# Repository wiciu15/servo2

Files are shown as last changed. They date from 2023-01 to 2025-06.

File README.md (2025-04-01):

# Servo 2
## 3-phase AC servomotor driver

This is a project of a servo inverter to drive 3-phase AC motor with/out encoder feedback

It's in alpha development so there are many bugs and things included in software but not really working/tested.

DEMO video: https://www.youtube.com/watch?v=Hu02lt5aCbM

CNC DEMO: https://www.youtube.com/watch?v=LXm4no8DIPE

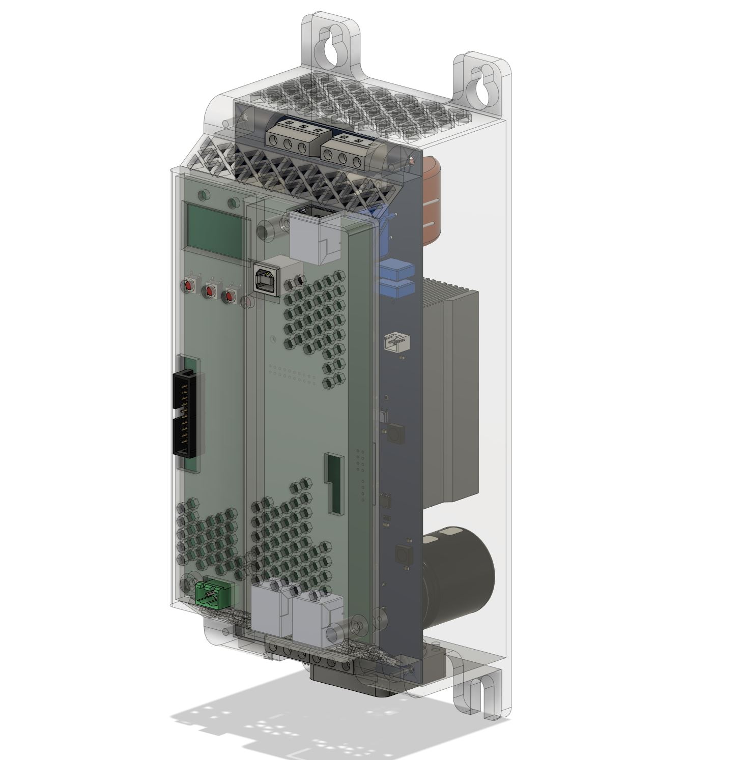
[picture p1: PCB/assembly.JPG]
CPU board


This is a free software under the GNU license, you can redistribute it and/or modify it under the terms
of the GNU General Public License version 3 as published by the Free Software Foundation.
This project is shared with public for educational purposes, without WARRANTY and Author is not liable for any damages caused directly
or indirectly by this software/hardware. The board is mains-powered. High voltage can kill you. Have caution when using high voltage devices

## Features

- Manual voltage and frequency control
- U/f scalar motor control
- Open loop current control for test purposes
- Field-oriented vector control (FOC) for PMSM/BLDC motors with encoder feedback
- Encoders support:
  -  ABZ encoder with differential driver output, needs one manual rotation to index with a rotor properly
  -  Mitsubishi J2/J2s/J4/JE series, baud rate 2 500 000 bits/s, implementation is working but need some polish
  -  Tamagawa T-Format encoders - tested with ABB BSM-series motor, baud rate 2 500 000 bits/s, most robust implementation and testing at this moment
  -  Panasonic minas series encoder - support in early development, not much tested and buggy
  -  DELTA NH4 series T+ T- encoder - very early development
- Braking chopper control
- under/overvoltage, overcurrent, short-circuit and other errors detection and handling
- Communication with PC using MODBUS over USB-CDC
- simple CANopen node for fieldbus control
- Parameter set, with non-volatile storage in external EEPROM
- control and monitoring of drive using OLED screen and buttons
- ramp generators and limiters for current,speed and position control loops

## To-do in the future

- I2t thermal monitoring of motor
- sensorless rotor angle aquisition
- analog and digital I/O
- step/dir input
- current and speed loop gains auto-tuning
- motor parameters automatic measurement

## Used third-party software
- I2C EEPROM driver by ControllersTech
- OLED driver https://github.com/afiskon/stm32-ssd1306
- stModbus https://github.com/wiciu15/stModbus/
- CANopenNode https://github.com/CANopenNode/CANopenNode
- embedded printf implementation https://github.com/mpaland/printf
- FreeRTOS

## Hardware modification
MOdifications of rev.A of CPU board
- data/command line to OLED screen(PA15)
- bridge between tim1break input (PE15) and overcurrent interrupt(PA1)(break interrupt was not working i dont know why just bridged it to EXTI on other pin).
- OLED CLK is moved to PA5, PB3 is used as DEBUG_SWO.
- added filter to GND on FAULT line from power board to enchance noise rejection from EMI(i was getting random short-circuit errors).

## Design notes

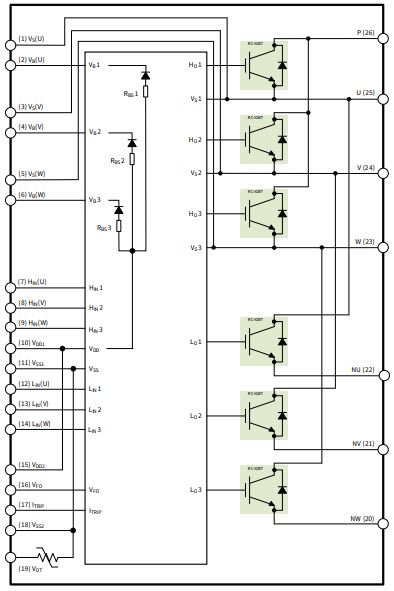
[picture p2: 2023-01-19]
PCB/servo_pwr/Infineon IPM.JPG

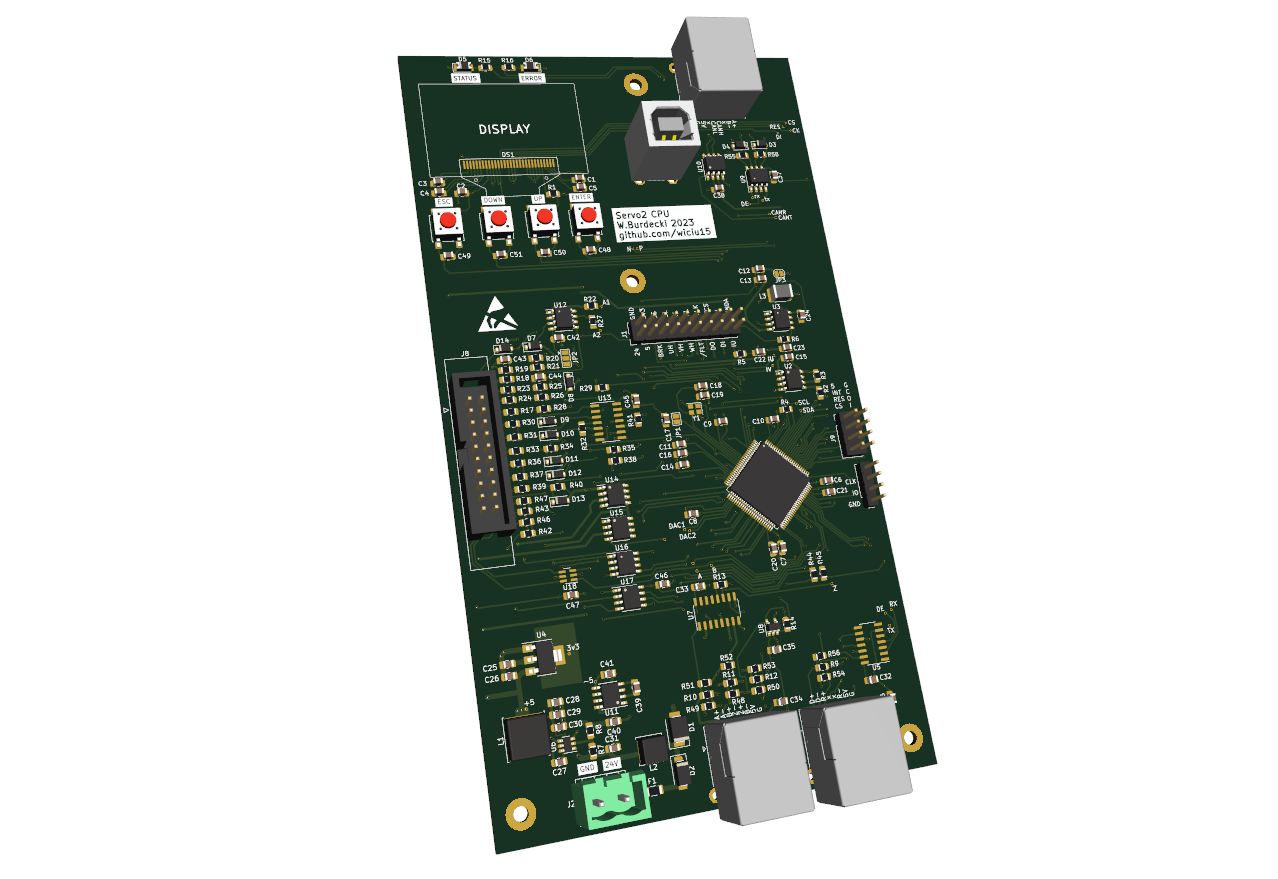
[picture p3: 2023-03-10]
PCB/servo_cpu/servo_cpu.png

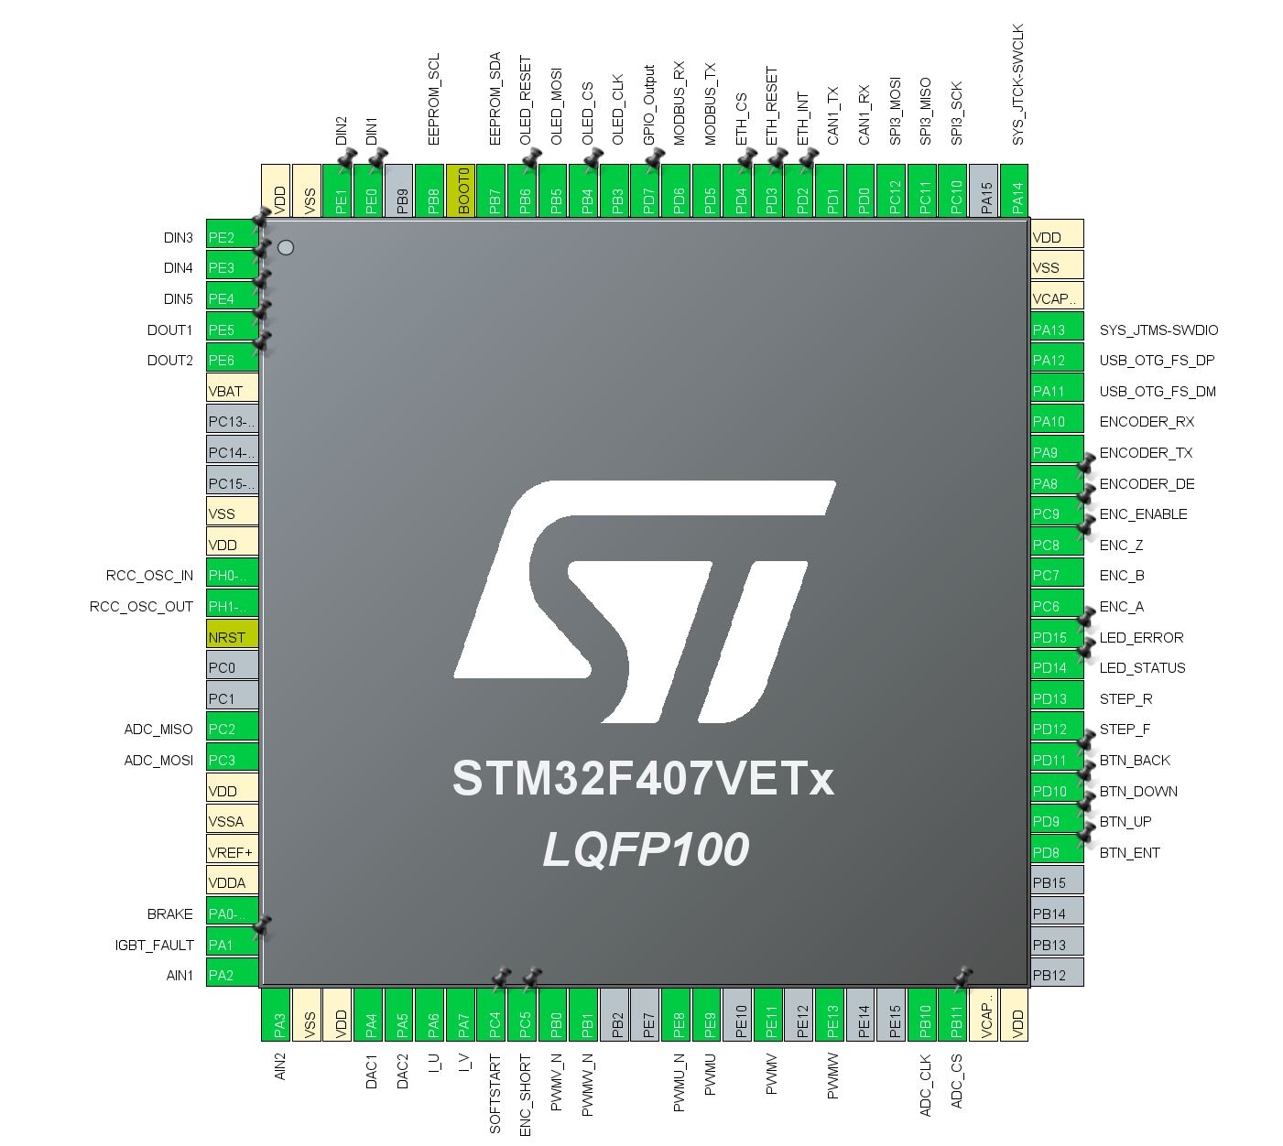
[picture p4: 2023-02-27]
PCB/servo_cpu/piny cpu.JPG

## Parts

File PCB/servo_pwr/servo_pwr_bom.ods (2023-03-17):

Designator | Name | Qt
C1, C3, C4, C5, C6, C7, C8, C11, C12, C13, C14, C15, C16, C17, C18, C19, C20, C21, C22, C23, C25, C30, C34, C36, C37 | 2.2 ﾵF | 25
C2, C9, C26, C27, C35 | 22 ﾵF | 5
C10 | 100 ﾵF | 1
C24 | 10000 pF | 1
C28, C32 | 4700 pF | 2
C29, C33 | 0.1 ﾵF | 2
C31 | 1000 pF | 1
C38 | 470n X2 275V | 1
C39, C40 | 470ﾵF | 2
C41, C42, C44, C45 | 4n7 | 4
C43 | 3.3u/600V | 1
D1 | 10A6 | 1
D2 | 1N4148W-7-F | 1
DB1 | Component_1 | 1
F1 | Fuse | 1
IC1 | LD1117S50TR | 1
IC2 | 2N7002E-7-F | 1
IPM1 | IM323L6G2 | 1
J1, J2, J3, J4 | DG128-7.5-03P-14 | 4
J5 | goldpin | 1
J6 | FAN | 1
J10 | jumper | 1
L1, L2 | 1 mH | 2
L3 | SC-18-25J | 1
MH3, MH4 | Mountinghole_M2,5 | 2
MH5, MH6, MH7, MH8 | Mountinghole_M2,5_nonplated | 4
Q1 | STGW30NC60KD | 1
R1, R2, R3, R4, R5, R6, R13, R20, R21, R22, R29 | 470 Ohms | 11
R7, R10 | 1 kOhms | 2
R8 | 22 kOhms | 1
R9, R25 | 47 Ohms | 2
R11, R12, R14 | 150 mOhms | 3
R15, R16, R17, R18 | 100 kOhms | 4
R19 | 4.7 kOhms | 1
R23, R24 | PRM05WJP333 | 2
R26 | 10 kOhms | 1
R27 | 1M | 1
R28 | PRMAAWJW470B00 | 1
RL1 | G2R-1A-E | 1
RV1 | SIOV-S20K275 | 1
TP1 | 5V | 1
TP2 | FO | 1
TP3 | HU | 1
TP4 | HV | 1
TP5 | HW | 1
TP8 | 15VH | 1
TP9 | OC | 1
TP10 | Gnd | 1
TP11 | 5VH | 1
TP12 | DO | 1
TP13 | G | 1
TP14 | IU | 1
TP15 | 3V3 | 1
TP16 | IV | 1
TP17 | TMP | 1
TP18 | CS | 1
TP19 | DI | 1
TP20 | CK | 1
U1, U3, U4, U5, U6, U7, U8, U9, U11, U13, U15 | TLP2345 | 11
U2 | TBA 2-0513 | 1
U10, U12 | LEM GO10SME/SP3 | 2
U14 | MCP3002-I/SN | 1
U16 | TLP701 | 1

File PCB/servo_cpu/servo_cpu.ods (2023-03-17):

C1, C2, C3, C4, C5, C6, C7, C8, C9, C10, C11, C12,C13, C14, C15, C16, C20, C21, C24, C25, C26, C32, C33, C34, C35, C36, C37, C38, C40, | 29 | 2u2
C17, C27, C42, C43, C44, C45, C46, C47, C48, C49, C50, C51, | 12 | 100n
C18, C19, | 2 | 12p
C22, C23, | 2 | 1u
C28, C29, C30, C31, C39, C41, | 6 | 22u
D1, | 1 | SM6T27A
D2, | 1 | US1B
D3, D4, | 2 | BZT52B6v2
D5, | 1 | GREEN_LED
D6, | 1 | RED_LED
D7, D8, D9, D10, D11, D12, D13, | 7 | BZT52B5v1
D14, | 1 | 1N4148
DS1, | 1 | OLED-128O064D
F1, | 1 | 615mA PTC
J1, | 1 | PWR board
J2, | 1 | Control power
J3, | 1 | ABZ
J4, | 1 | Serial Encoder
J5, | 1 | CONN
J6, | 1 | DEBUG
J7, | 1 | USB_B
J8, | 1 | I/O
J9, | 1 | EXT
JP1, | 1 | RESET
JP2, | 1 | OPA-V
JP3, | 1 | GND
L1, | 1 | 4u7
L2, | 1 | 10u
L3, | 1 | 470u
R1, | 1 | 820k
R2, R3, | 2 | 4,7k
R4, R15, R16, R44, R45, R55, | 6 | 1k
R5, R6, | 2 | 22R
R7, | 1 | 220k
R8, | 1 | 18k
R9, R22, R27, | 3 | 150R
R10, R11, R12, | 3 | 220R
R13, R14, R17, R18, R19, R23, R24, R29, R30, R32, R33, R35, R36, R38, R39, R41, | 16 | 10k
R20, R21, R25, R26, | 4 | 3k3
R28, R31, R34, R37, R40, R42, R43, | 7 | 2k2
R46, R47, R48, R49, R50, R51, R52, R53, R54, R56, R58, | 11 | 470R
SW1, | 1 | ENTER
SW2, | 1 | ESC
SW3, | 1 | UP
SW4, | 1 | DOWN
U1, | 1 | STM32F407VETx
U2, | 1 | M24C02-WMN
U3, U12, U16, | 3 | TS912
U4, | 1 | AP1117-33
U5, | 1 | ISL83491
U6, | 1 | AP63205WU
U7, | 1 | AM26LS32A
U8, | 1 | AP2151A
U9, | 1 | MAX485E
U10, | 1 | SN65HVD232
U11, | 1 | LMC7660
U13, | 1 | 74HC14
U14, U15, | 2 | ISP742RI
U17, | 1 | VO0661T
U18, | 1 | 74LVC2G04
Y1, | 1 | 16M xt224

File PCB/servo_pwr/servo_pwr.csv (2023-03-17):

Line # | Designator | Name | Quantity | Description | Manufacturer 1 | Manufacturer Part Number 1 | Manufacturer Lifecycle 1 | Supplier 1 | Supplier Part Number 1 | Supplier Unit Price 1 | Supplier Subtotal 1
 | C1, C3, C4, C5, C6, C7, C8, C11, C12, C13, C14, C15, C16, C17, C18, C19, C20, C21, C22, C23, C25, C30, C34, C36, C37 | 2.2 µF | 25 | CAP CER 2.2UF 35V X7R 0805 | TDK | C2012X7R1V225K125AB | Volume Production | Digi-Key | 445-7551-1-ND | 0.373 | 9.33
 | C2, C9, C26, C27, C35 | 22 µF | 5 | CAP CER 22UF 16V X5R 0805 | Samsung | CL21A226KOQNNNG | Volume Production | Digi-Key | 1276-7092-1-ND | 0.33 | 1.65
 | C10 | 100 µF | 1 | CAP ALUM 100UF 20% 25V RADIAL | Panasonic | EEUTA1E101 | Volume Production | DigiKey | P19501-ND
 | C24 | 10000 pF | 1 | CAP CER 0805 10NF 50V X7R 10% | KEMET | C0805C103K5RECAUTO | Unknown | Digi-Key | 399-17885-1-ND | 0.25 | 0.25
 | C28, C32 | 4700 pF | 2 | CAP CER 0805 4.7NF 50V X7R 10% | KEMET | C0805C472K5RECAUTO | Unknown | DigiKey | 399-17884-1-ND
 | C29, C33 | 0.1 µF | 2 | CAP CER 0.1UF 50V X7R 0805 | Yageo | CC0805MRX7R9BB104 | Volume Production | Digi-Key | 311-4351-1-ND | 0.13 | 0.26
 | C31 | 1000 pF | 1 | CAP CER 0805 1NF 50V ULTRA STABL | KEMET | C0805X102J5HACAUTO | Unknown | Digi-Key | 399-16876-1-ND | 0.22 | 0.22
 | C38 | 470n X2 275V | 1 | KEMET R46KI347050M1K
 | C39, C40 | 470µF | 2 | CAP ALUM 470UF 20% 450V SNAP | Rubycon | 450HXG470MEFCSN35X45 | Volume Production | Digi-Key | 1189-1975-ND | 11.39 | 22.78
 | C41, C42, C44, C45 | 4n7 | 4 | B32021A3472
 | C43 | 3.3u/600V | 1
 | D1 | 10A6 | 1
 | D2 | 1N4148W-7-F | 1 | DIODE GEN PURP 100V 300MA SOD123 | Diodes | 1N4148W-7-F | Unknown | Digi-Key | 1N4148W-FDICT-ND | 0.17 | 0.17
 | DB1 | Component_1 | 1
 | F1 | Fuse | 1 | Fuse holder 04450001N
 | IC1 | LD1117S50TR | 1 | IC REG LINEAR 5V 800MA SOT223 | STMicroelectronics | LD1117S50TR | Unknown | Digi-Key | 497-6447-1-ND | 0.66 | 0.66
 | IC2 | 2N7002E-7-F | 1 | MOSFET N-CH 60V 0.25A SOT23-3 | Diodes | 2N7002E-7-F | Volume Production | DigiKey | 2N7002E-FDICT-ND
 | IPM1 | IM323L6G2 | 1
 | J1, J2, J3, J4 | DG128-7.5-03P-14 | 4
 | J5 | goldpin | 1
 | J6 | FAN | 1
 | J10 | jumper | 1
 | L1, L2 | 1 mH | 2 | FIXED IND 1MH 150MA 4.5 OHM SMD | Bourns | SRR6028-102Y | Volume Production | DigiKey | SRR6028-102YCT-ND
 | L3 | SC-18-25J | 1 | https://www.tme.eu/pl/details/sc-18-25j/dlawiki-pierscieniowe/kemet/
 | MH3, MH4 | Mountinghole_M2,5 | 2
 | MH5, MH6, MH7, MH8 | Mountinghole_M2,5_nonplated | 4
 | Q1 | STGW30NC60KD | 1
 | R1, R2, R3, R4, R5, R6, R13, R20, R21, R22, R29 | 470 Ohms | 11 | RES SMD 470 OHM 0.1% 1/4W 0805 | Panasonic | ERJ-PB6B4700V | New Product | Digi-Key | P20556CT-ND | 0.338 | 3.72
 | R7, R10 | 1 kOhms | 2 | RES 1K OHM 0.1% 1/10W 0805 | Stackpole Electronics | RNCS0805BKE1K00 | Volume Production | Digi-Key | RNCS0805BKE1K00CT-ND | 0.52 | 1.04
 | R8 | 22 kOhms | 1 | RES 22K OHM 5% 1/8W 0805 | TE Connectivity | CRGCQ0805J22K | Unknown | Digi-Key | A130142CT-ND | 0.1 | 0.1
 | R9, R25 | 47 Ohms | 2 | RES 47 OHM 1% 1/3W 0805 | TE Connectivity | CRGP0805F47R | Unknown | Digi-Key | A130461CT-ND | 0.22 | 0.44
 | R11, R12, R14 | 150 mOhms | 3 | RES 150M OHM 1% 2W 2512 | KOA Speer | TLRH3AWTTER150F | Volume Production | Digi-Key | 2019-TLRH3AWTTER150FCT-ND | 1.48 | 4.44
 | R15, R16, R17, R18 | 100 kOhms | 4 | RES SMD 100K OHM 0.1% 1/4W 1206 | Yageo | RT1206BRB07100KL | Volume Production | Digi-Key | YAG5016CT-ND | 0.75 | 3
 | R19 | 4.7 kOhms | 1 | RES SMD 4.7K OHM 1% 1/4W 1206 | TE Connectivity | CRG1206F4K7 | Volume Production | Digi-Key | A106078CT-ND | 0.1 | 0.1
 | R23, R24 | PRM05WJP333 | 2
 | R26 | 10 kOhms | 1 | RES 10K OHM 0.1% 1/10W 0805 | Stackpole Electronics | RNCS0805BKE10K0 | Volume Production | Digi-Key | RNCS0805BKE10K0CT-ND | 0.52 | 0.52
 | R27 | 1M | 1 | Resistor
 | R28 | PRMAAWJW470B00 | 1 | https://www.tme.eu/pl/details/ax10wv-47r/rezystory-mocy/royal-ohm/prmaawjw470b00/
 | RL1 | G2R-1A-E | 1 | https://www.tme.eu/pl/details/g2r-1a-e-24dc/przekazniki-elektromagn-miniaturowe/omron-ocb/g2r-1a-e-24vdc/
 | RV1 | SIOV-S20K275 | 1 | B72220S0271K101
 | TP1 | 5V | 1
 | TP2 | FO | 1
 | TP3 | HU | 1
 | TP4 | HV | 1
 | TP5 | HW | 1
 | TP8 | 15VH | 1
 | TP9 | OC | 1
 | TP10 | Gnd | 1
 | TP11 | 5VH | 1
 | TP12 | DO | 1
 | TP13 | G | 1
 | TP14 | IU | 1
 | TP15 | 3V3 | 1
 | TP16 | IV | 1
 | TP17 | TMP | 1
 | TP18 | CS | 1
 | TP19 | DI | 1
 | TP20 | CK | 1
 | U1, U3, U4, U5, U6, U7, U8, U9, U11, U13, U15 | TLP2345 | 11
 | U2 | TBA 2-0513 | 1 | No Description Available
 | U10, U12 | LEM GO10SME/SP3 | 2
 | U14 | MCP3002-I/SN | 1 | No Description Available
 | U16 | TLP701 | 1

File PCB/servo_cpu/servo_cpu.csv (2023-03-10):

Source: | C:\Users\Wiktor\Documents\servo2pcb\PCB\servo_cpu\servo_cpu.kicad_sch
Date: | 10.03.2023 15:43:41
Tool: | Eeschema (7.0.0)
Generator: | C:\Program Files\KiCad\6.0\bin\scripting\plugins/bom_csv_grouped_by_value_with_fp.py
Component Count: | 162
Ref | Qnty | Value | Cmp name | Footprint | Description | Vendor
C1, C2, C3, C4, C5, C6, C7, C8, C9, C10, C11, C12, C13, C14, C15, C16, C20, C21, C24, C25, C26, C32, C33, C34, C35, C36, C37, C38, C40, | 29 | 2u2 | C_Small | Capacitor_SMD:C_0805_2012Metric_Pad1.18x1.45mm_HandSolder | Unpolarized capacitor, small symbol
C17, C27, C42, C43, C44, C45, C46, C47, C48, C49, C50, C51, | 12 | 100n | C_Small | Capacitor_SMD:C_0805_2012Metric_Pad1.18x1.45mm_HandSolder | Unpolarized capacitor, small symbol
C18, C19, | 2 | 12p | C_Small | Capacitor_SMD:C_0805_2012Metric_Pad1.18x1.45mm_HandSolder | Unpolarized capacitor, small symbol
C22, C23, | 2 | 1u | C_Small | Capacitor_SMD:C_0805_2012Metric_Pad1.18x1.45mm_HandSolder | Unpolarized capacitor, small symbol
C28, C29, C30, C31, C39, C41, | 6 | 22u | C_Small | Capacitor_SMD:C_0805_2012Metric_Pad1.18x1.45mm_HandSolder | Unpolarized capacitor, small symbol
D1, | 1 | SM6T27A | SM6T27A | Diode_SMD:D_SMB | 600W unidirectional Transil Transient Voltage Suppressor, 27Vrwm, DO-214AA
D2, | 1 | US1B | US1B | Diode_SMD:D_SMA | 100V, 1A, General Purpose Rectifier Diode, SMA(DO-214AC)
D3, D4, | 2 | BZT52B6v2 | BZT52Bxx | Diode_SMD:D_SOD-123F | 500mW Zener Diode, SOD-123F
D5, | 1 | GREEN_LED | LED | Diode_SMD:D_1206_3216Metric_Pad1.42x1.75mm_HandSolder | Light emitting diode
D6, | 1 | RED_LED | LED | Diode_SMD:D_1206_3216Metric_Pad1.42x1.75mm_HandSolder | Light emitting diode
D7, D8, D9, D10, D11, D12, D13, | 7 | BZT52B5v1 | BZT52Bxx | Diode_SMD:D_SOD-123F | 500mW Zener Diode, SOD-123F
D14, | 1 | 1N4148 | D_Small | Diode_SMD:D_SOD-123F | Diode, small symbol
DS1, | 1 | OLED-128O064D | OLED-128O064D | Display:OLED-128O064D | OLED display 128x64
F1, | 1 | 615mA PTC | Fuse | Fuse:Fuse_1206_3216Metric | Fuse
J1, | 1 | PWR board | Conn_02x10_Counter_Clockwise | Connector_PinHeader_2.54mm:PinHeader_2x10_P2.54mm_Vertical | Generic connector, double row, 02x10, counter clockwise pin numbering scheme (similar to DIP package numbering), script generated (kicad-library-utils/schlib/autogen/connector/)
J2, | 1 | Control power | Screw_Terminal_01x02 | TerminalBlock_RND:TerminalBlock_RND_205-00232_1x02_P5.08mm_Horizontal | Generic screw terminal, single row, 01x02, script generated (kicad-library-utils/schlib/autogen/connector/)
J3, | 1 | ABZ | 8P8C_Shielded | Connector_RJ:RJ45_Ninigi_GE | RJ connector, 8P8C (8 positions 8 connected), RJ31/RJ32/RJ33/RJ34/RJ35/RJ41/RJ45/RJ49/RJ61, Shielded
J4, | 1 | Serial Encoder | 8P8C_Shielded | Connector_RJ:RJ45_Ninigi_GE | RJ connector, 8P8C (8 positions 8 connected), RJ31/RJ32/RJ33/RJ34/RJ35/RJ41/RJ45/RJ49/RJ61, Shielded
J5, | 1 | CONN | 8P8C_Shielded | Connector_RJ:RJ45_Ninigi_GE | RJ connector, 8P8C (8 positions 8 connected), RJ31/RJ32/RJ33/RJ34/RJ35/RJ41/RJ45/RJ49/RJ61, Shielded
J6, | 1 | DEBUG | Conn_01x04 | Connector_PinHeader_2.54mm:PinHeader_1x04_P2.54mm_Vertical | Generic connector, single row, 01x04, script generated (kicad-library-utils/schlib/autogen/connector/)
J7, | 1 | USB_B | USB_B | USB_B_JST_Vertical:USB | USB Type B connector
J8, | 1 | I/O | Conn_02x10_Odd_Even | Connector_IDC:IDC-Header_2x10_P2.54mm_Latch_Vertical | Generic connector, double row, 02x10, odd/even pin numbering scheme (row 1 odd numbers, row 2 even numbers), script generated (kicad-library-utils/schlib/autogen/connector/)
J9, | 1 | EXT | Conn_02x04_Odd_Even | Connector_PinHeader_2.54mm:PinHeader_2x04_P2.54mm_Horizontal | Generic connector, double row, 02x04, odd/even pin numbering scheme (row 1 odd numbers, row 2 even numbers), script generated (kicad-library-utils/schlib/autogen/connector/)
JP1, | 1 | RESET | SolderJumper_2_Open | Jumper:SolderJumper-2_P1.3mm_Open_Pad1.0x1.5mm | Solder Jumper, 2-pole, open
JP2, | 1 | OPA-V | SolderJumper_3_Bridged12 | Jumper:SolderJumper-3_P1.3mm_Bridged12_Pad1.0x1.5mm | 3-pole Solder Jumper, pins 1+2 closed/bridged
JP3, | 1 | GND | Jumper_2_Bridged | Jumper:SolderJumper-2_P1.3mm_Bridged_RoundedPad1.0x1.5mm | Jumper, 2-pole, closed/bridged
L1, | 1 | 4u7 | L_Small | Inductor_SMD:L_Sunlord_SWPA8040S | Inductor, small symbol
L2, | 1 | 10u | L_Small | Inductor_SMD:L_Sunlord_SWPA5040S | Inductor, small symbol
L3, | 1 | 470u | L_Small | Inductor_SMD:L_1812_4532Metric_Pad1.30x3.40mm_HandSolder | Inductor, small symbol
R1, | 1 | 820k | R_Small | Resistor_SMD:R_0805_2012Metric_Pad1.20x1.40mm_HandSolder | Resistor, small symbol
R2, R3, | 2 | 4,7k | R_Small | Resistor_SMD:R_0805_2012Metric_Pad1.20x1.40mm_HandSolder | Resistor, small symbol
R4, R15, R16, R44, R45, R55, | 6 | 1k | R_Small | Resistor_SMD:R_0805_2012Metric_Pad1.20x1.40mm_HandSolder | Resistor, small symbol
R5, R6, | 2 | 22R | R_Small | Resistor_SMD:R_0805_2012Metric_Pad1.20x1.40mm_HandSolder | Resistor, small symbol
R7, | 1 | 220k | R_Small | Resistor_SMD:R_0805_2012Metric_Pad1.20x1.40mm_HandSolder | Resistor, small symbol
R8, | 1 | 18k | R_Small | Resistor_SMD:R_0805_2012Metric_Pad1.20x1.40mm_HandSolder | Resistor, small symbol
R9, R22, R27, | 3 | 150R | R_Small | Resistor_SMD:R_0805_2012Metric_Pad1.20x1.40mm_HandSolder | Resistor, small symbol
R10, R11, R12, | 3 | 220R | R_Small | Resistor_SMD:R_0805_2012Metric_Pad1.20x1.40mm_HandSolder | Resistor, small symbol
R13, R14, R17, R18, R19, R23, R24, R29, R30, R32, R33, R35, R36, R38, R39, R41, | 16 | 10k | R_Small | Resistor_SMD:R_0805_2012Metric_Pad1.20x1.40mm_HandSolder | Resistor, small symbol
R20, R21, R25, R26, | 4 | 3k3 | R_Small | Resistor_SMD:R_0805_2012Metric_Pad1.20x1.40mm_HandSolder | Resistor, small symbol
R28, R31, R34, R37, R40, R42, R43, | 7 | 2k2 | R_Small | Resistor_SMD:R_0805_2012Metric_Pad1.20x1.40mm_HandSolder | Resistor, small symbol
R46, R47, R48, R49, R50, R51, R52, R53, R54, R56, R58, | 11 | 470R | R_Small | Resistor_SMD:R_0805_2012Metric_Pad1.20x1.40mm_HandSolder | Resistor, small symbol
SW1, | 1 | ENTER | SW_Push | Button_Switch_SMD:SW_SPST_B3S-1000 | Push button switch, generic, two pins
SW2, | 1 | ESC | SW_Push | Button_Switch_SMD:SW_SPST_B3S-1000 | Push button switch, generic, two pins
SW3, | 1 | UP | SW_Push | Button_Switch_SMD:SW_SPST_B3S-1000 | Push button switch, generic, two pins
SW4, | 1 | DOWN | SW_Push | Button_Switch_SMD:SW_SPST_B3S-1000 | Push button switch, generic, two pins
U1, | 1 | STM32F407VETx | STM32F407VETx | Package_QFP:LQFP-100_14x14mm_P0.5mm | STMicroelectronics Arm Cortex-M4 MCU, 512KB flash, 192KB RAM, 168 MHz, 1.8-3.6V, 82 GPIO, LQFP100
U2, | 1 | M24C02-WMN | M24C02-WMN | Package_SO:SOIC-8_3.9x4.9mm_P1.27mm | 2Kb (256x8) I2C Serial EEPROM, 2.5-5.5V, SOIC-8
U3, U12, U16, | 3 | TS912 | TS912 | Package_SO:SO-8_3.9x4.9mm_P1.27mm | Dual Rail-to-rail CMOS Operational Amplifier, DIP-8/SOIC-8
U4, | 1 | AP1117-33 | AP1117-33 | Package_TO_SOT_SMD:SOT-223-3_TabPin2 | 1A Low Dropout regulator, positive, 3.3V fixed output, SOT-223
U5, | 1 | ISL83491 | ISL83491 | Package_SO:SO-14_3.9x8.65mm_P1.27mm | 10Mbps RS485/RS422 transceiver, full duplex, receiver/driver enable, low power shutdown
U6, | 1 | AP63205WU | AP63205WU | Package_TO_SOT_SMD:TSOT-23-6 | 2A, 1.1MHz Buck DC/DC Converter, fixed 5.0V output voltage, TSOT-23-6
U7, | 1 | AM26LS32A | AM26LS32A | Package_SO:SO-16_3.9x9.9mm_P1.27mm
U8, | 1 | AP2151A | AP2171W | Package_TO_SOT_SMD:SOT-23-5 | Current limited power switch, single channel, SOT-23-5
U9, | 1 | MAX485E | MAX485E | Package_SO:SO-8_3.9x4.9mm_P1.27mm | Half duplex RS-485/RS-422, 2.5 Mbps, Â±15kV electro-static discharge (ESD) protection, no slew-rate, no low-power shutdown, with receiver/driver enable, 32 receiver drive kapacitity, DIP-8 and SOIC-8
U10, | 1 | SN65HVD232 | SN65HVD232 | Package_SO:SOIC-8_3.9x4.9mm_P1.27mm | CAN Bus Transceivers, 3.3V, 1Mbps, SOIC-8
U11, | 1 | LMC7660 | LMC7660 | Package_SO:SOIC-8_3.9x4.9mm_P1.27mm | Voltage converter from +1.5V to +10V to +1.5V to +10V, SO-8/DIP-8
U13, | 1 | 74HC14 | 74HC14 | Package_SO:SO-14_3.9x8.65mm_P1.27mm | Hex inverter schmitt trigger
U14, U15, | 2 | ISP742RI | ISP742 | Package_SO:SOIC-8_3.9x4.9mm_P1.27mm
U17, | 1 | VO0661T | VO0661T | Package_SO:SOIC-8_3.9x4.9mm_P1.27mm | Dual High Speed CMOS Compatible Optocoupler, dV/dt 15000/us, VCM 1000, max 7V VCC, SOIC-8
U18, | 1 | 74LVC2G04 | 74LVC2G04 | Package_SO:SC-74-6_1.5x2.9mm_P0.95mm | Dual NOT Gate, Low-Voltage CMOS
Y1, | 1 | 16M xt224 | Crystal_GND24_Small | Crystal:Crystal_SMD_2520-4Pin_2.5x2.0mm | Four pin crystal, GND on pins 2 and 4, small symbol

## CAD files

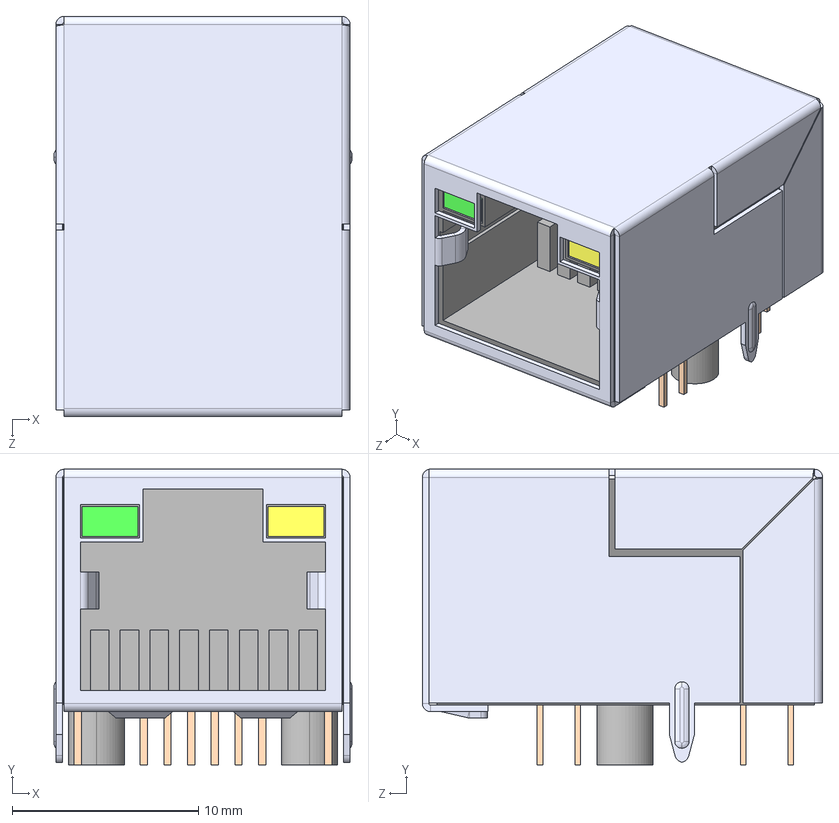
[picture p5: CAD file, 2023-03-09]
PCB/servo_cpu/RJ45_10P_TJ3009.STEP
16.0 x 15.9 x 21.5 mm

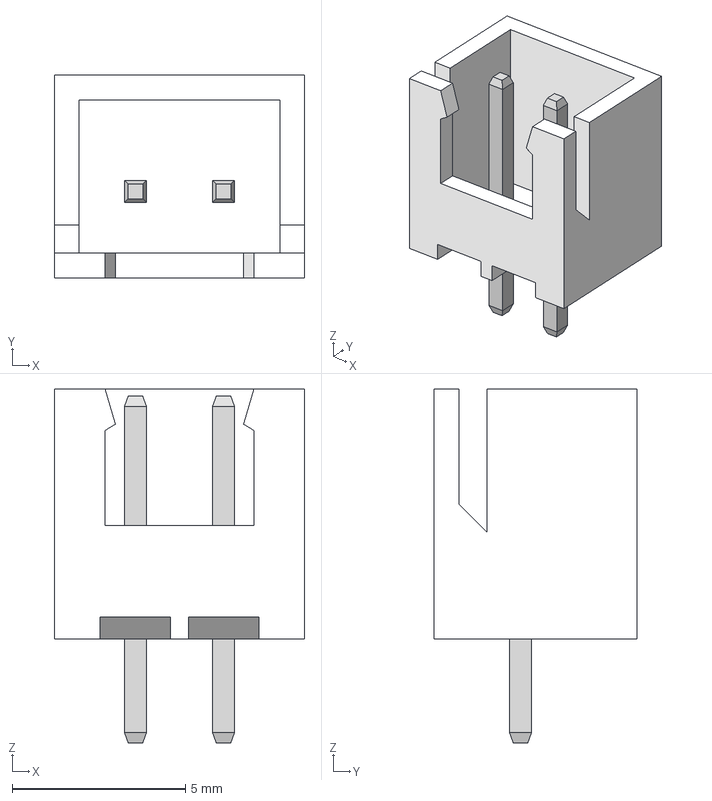
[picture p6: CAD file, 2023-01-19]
PCB/servo_pwr/connector/JST - XH - Thru (V) - 2Pin - 2.54mm.stp
7.21 x 5.84 x 10.2 mm

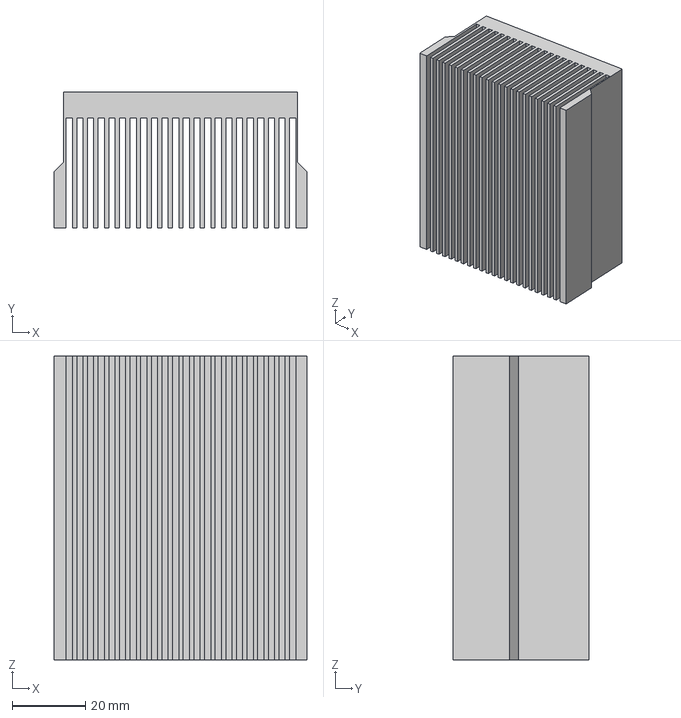
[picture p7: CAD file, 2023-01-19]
PCB/servo_pwr/radiator v1.step
69.0 x 37.0 x 83.0 mm

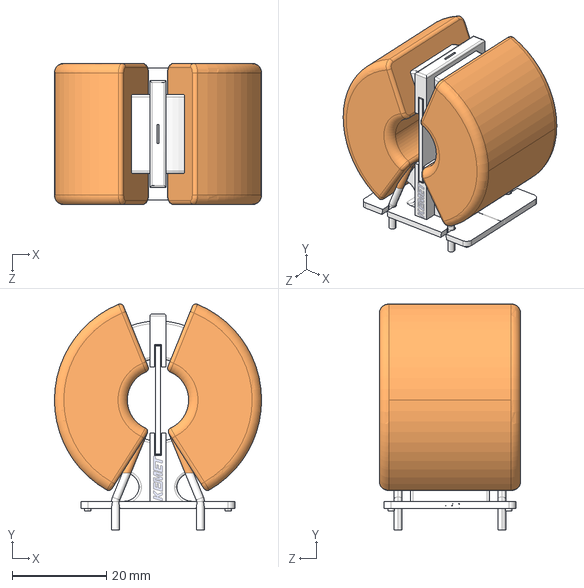
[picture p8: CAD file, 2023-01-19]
PCB/servo_pwr/SC-18-25J/SC-18-25J.step
44.0 x 48.0 x 30.0 mm

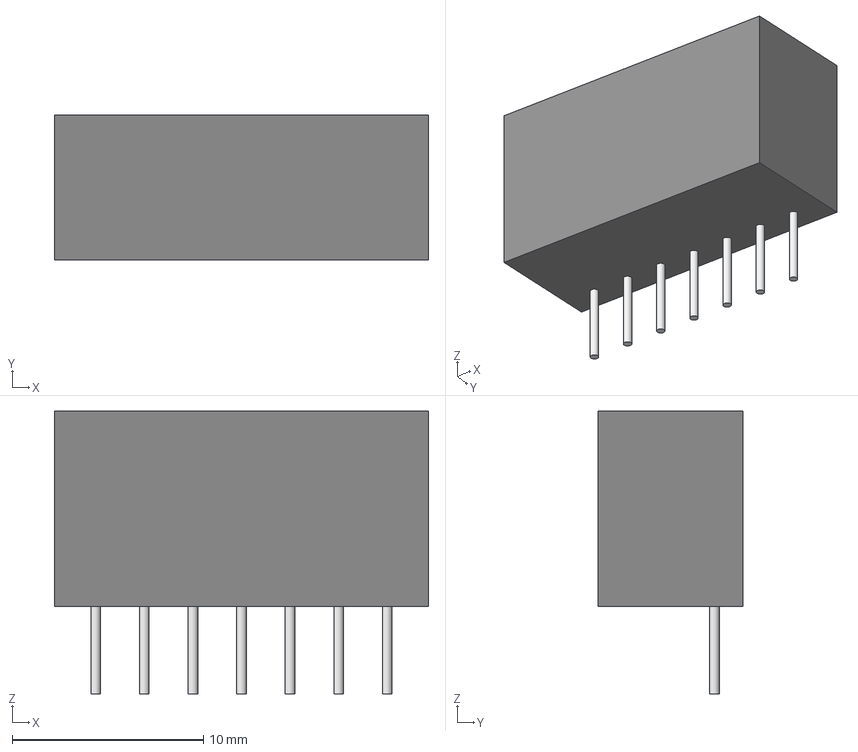
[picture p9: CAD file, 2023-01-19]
PCB/servo_pwr/TBA2-0513/TBA2_SINGLE_TRP.step
19.6 x 7.59 x 14.8 mm

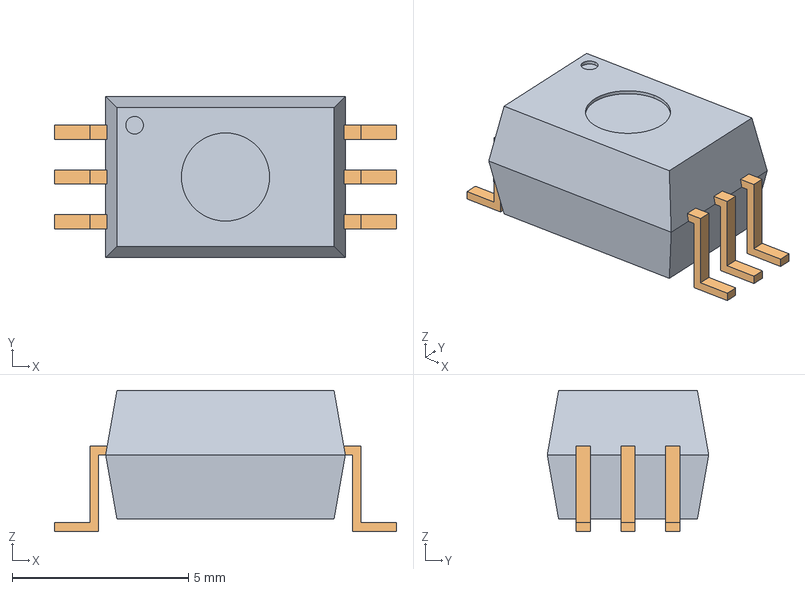
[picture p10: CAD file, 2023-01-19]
PCB/servo_pwr/Toshiba opto/SDIP6_90deg.stp
9.70 x 4.58 x 4.00 mm

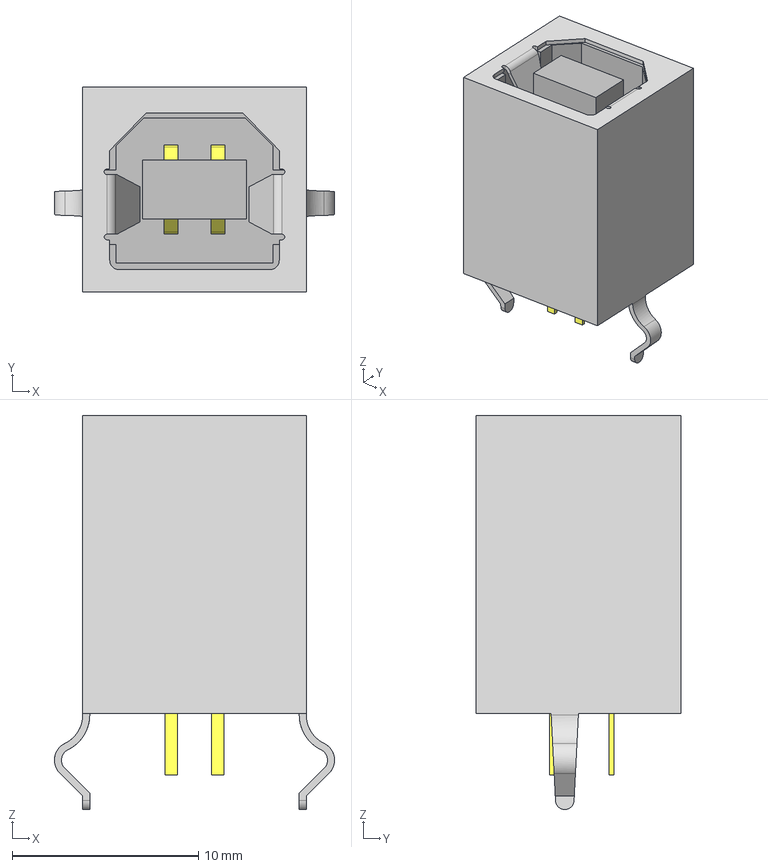
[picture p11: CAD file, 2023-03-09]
PCB/servo_cpu/USB-B-S-F-B-VT.stp
15.0 x 11.0 x 21.1 mm
USB-B-S-VT_P
USB-B-S-B-VT_B
USB-B-S-VT_S

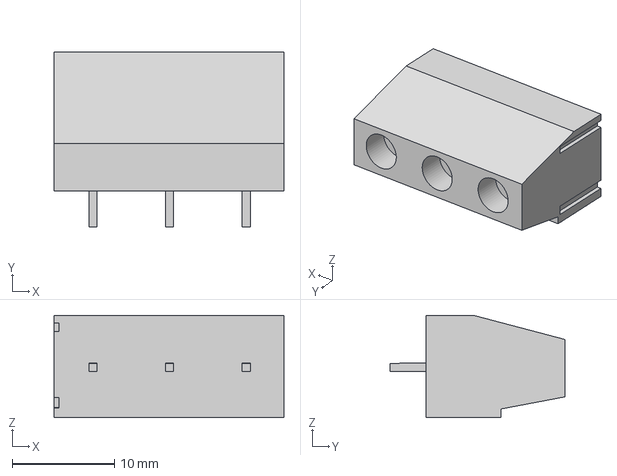
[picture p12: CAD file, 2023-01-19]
PCB/servo_pwr/connector/degson 3pin v1.step
22.5 x 17.1 x 10.0 mm

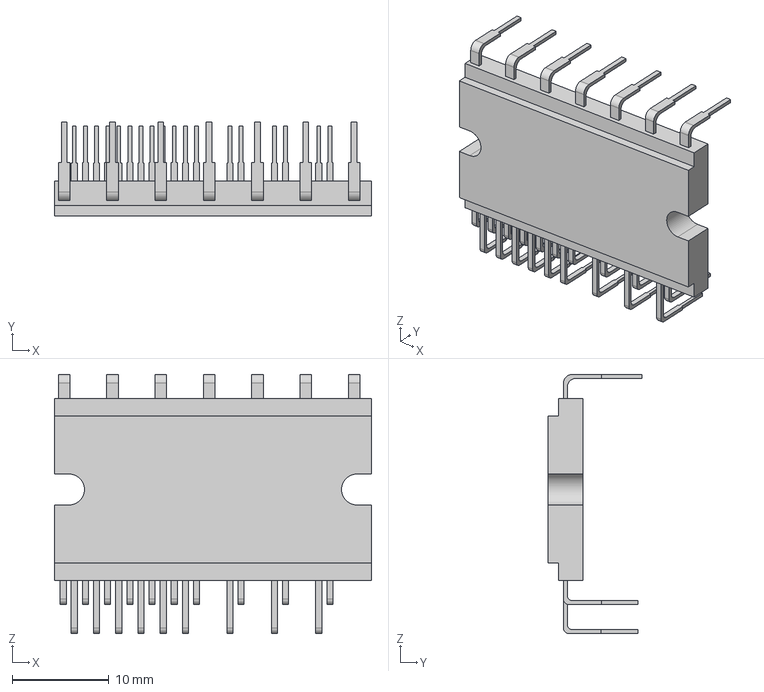
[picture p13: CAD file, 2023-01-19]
PCB/servo_pwr/Infineon IPM.step
32.8 x 9.68 x 26.8 mm

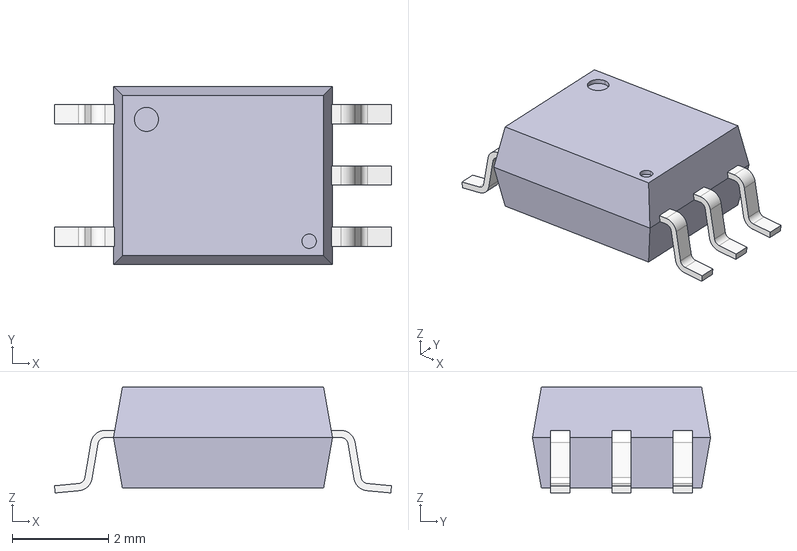
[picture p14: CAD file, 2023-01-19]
PCB/servo_pwr/Toshiba opto/5pin_SO6_z90.stp
7.00 x 3.70 x 2.20 mm

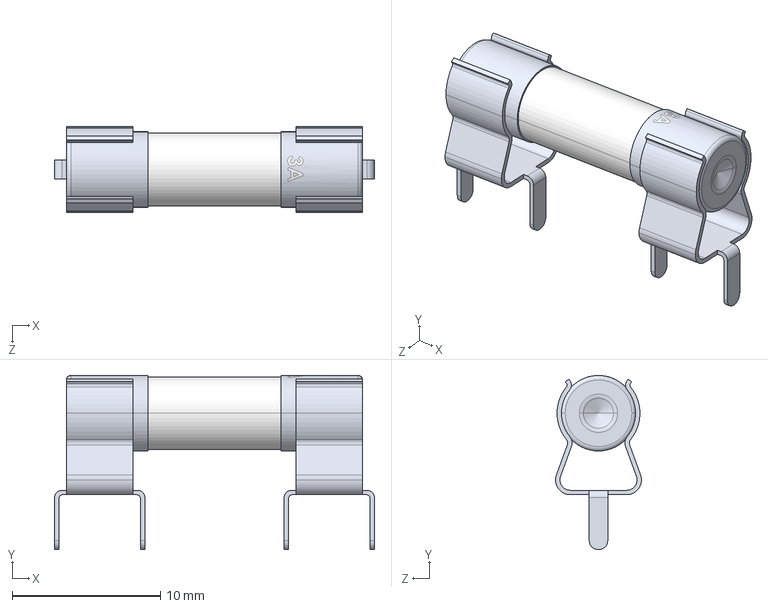
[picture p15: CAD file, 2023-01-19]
PCB/servo_pwr/Fuse Holder.STEP
21.6 x 11.8 x 5.80 mm
Fuse Clip x 2
3A Fuse

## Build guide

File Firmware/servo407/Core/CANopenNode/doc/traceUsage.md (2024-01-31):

Trace usage
===========

**TRACE DOES NOT WORK IN THE LAST VERSION**

CANopenNode includes optional trace functionality (non-standard). It monitors
choosen variables from Object Dictionary. On change of state of variable it
makes a record with timestamp into circular buffer. String with points can later
be read via SDO.

Trace is disabled by default. It can be enabled using Object Dictionary editor.
Include also *CO_trace.h/.c* into project, compile and run.

Here is en example of monitoring variable, connected with buttons
(OD_readInput8Bit, index 0x6000, subindex 0x01). It was tested on PIC32:

```
# Enable trace first:
./canopencomm 0x30 w 0x2400 0 u8 1

# Press and hold the button on Explorer16 and execute SDO read command:
./canopencomm 0x30 r 0x6000 1 u8
[1] 0x08
# It displays same value, as was transmitted via PDO and visible on candump.

# Now get the complete history for that buttons with timestamp for each change
# and store it as a text to the file:
./canopencomm 0x30 r 0x2401 5 vs > plot1.csv
cat plot1.csv
```
If large data blocks are transmitted via CAN bus, then more efficient SDO block
transfer can be enabled with command `./canopencomm set sdo_block 1`

For more info on using trace functionality see CANopenNode/example/IO.html
file. There is also a description of all Object Dictionary variables.

Trace functionality can also be configured on CANopenSocket directly. In that
case CANopenSocket must first receive PDO data from remote node(s) and store it
to the local Object Dictionary variable. CANopenSocket's trace then monitors
that variable. Text buffer is then read with the similar command as above. But
local SDO data access from CANopenSocket itself doesn't occupy CAN bus, so large
data is transfered realy fast. Besides that, Linux machine has much more RAM to
store the monitored data. Except timestamp is less accurate.

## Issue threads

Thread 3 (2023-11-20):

Change the igbt driver with IKCM30F60GA

artayasa, 2023-11-20:
Hi sir, im interest with your project.
It is posible to change the igbtdriver with this chip, IKCM30F60GA. I see datasheet almost same.
And also this suport step/dir control??
If suport can i not use some things to save the space?? I just want to used ac servo pmsm with abz encorder 2500ppr.

wiciu15, 2023-11-20:
Pinout is the same so should work, overcurrent limit could be set higher because igbt's are 30A max instead of 20A. Thermally i think it would perform similarly.

Positioning control mode and  step/dir input is not implemented yet, only speed/torque control.

wiciu15, 2023-11-20:
On second look NTC pin does not exist so igbt temperature would not work and 2 power supply pins are not there you would have to bend following pins 2 holes forward

artayasa, 2023-11-20:
> On second look NTC pin does not exist so igbt temperature would not work and 2 power supply pins are not there you would have to bend following pins 2 holes forward

What do u mean sir??? Mybei will used external ntc sirr

artayasa, 2024-07-18:
> On second look NTC pin does not exist so igbt temperature would not work and 2 power supply pins are not there you would have to bend following pins 2 holes forward

For now step dir are apply sir? Because i see demo cnc with grbl, i think it control by step/dir??

artayasa, 2024-07-18:
> I made some progress but it's still buggy, and needs hardware modification on board. czw., 18 lip 2024, 22:03 użytkownik artayasa ***@***.***> napisał:
> […](#)
> On second look NTC pin does not exist so igbt temperature would not work and 2 power supply pins are not there you would have to bend following pins 2 holes forward For now step dir are apply sir? Because i see demo cnc with grbl, i think it control by step/dir?? — Reply to this email directly, view it on GitHub <[#3 (comment)](https://github.com/wiciu15/servo2/issues/3#issuecomment-2237466003)>, or unsubscribe <https://github.com/notifications/unsubscribe-auth/AI7OJSG6WXH22LYDM6OOY2TZNANPJAVCNFSM6AAAAABLDKZVUKVHI2DSMVQWIX3LMV43OSLTON2WKQ3PNVWWK3TUHMZDEMZXGQ3DMMBQGM> . You are receiving this because you commented.Message ID: ***@***.***>

Owhh okee sirr, and also i have more ex broken ac servo drive in home, i will modify it to used your frimeware and coustem the board. But to hard buy curent shunt G010SME-SP3. It posible to used acs712?? Without curent aplifier?? Because all ofthat i have already. And my servo is 2pcs 100v, 5 pcs 200v. How do u control the voltage? By software??

And also about the software where i can get it?? I dont see in your github. Thank u for the great project.

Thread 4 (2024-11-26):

Where we can download or get the software

artayasa, 2024-11-26:
Hi mate where we can get the software, i wan to try your code.

wiciu15, 2024-11-26:
Clone the repo or use green download as zip button

artayasa, 2024-11-26:
> Clone the repo or use green download as zip button

Yes but i dont see the software for setting like u sir. Its not open source??

wiciu15, 2024-11-26:
I can't share PC application due to licensing of internal components

artayasa, 2024-11-26:
> I can't share PC application due to licensing of internal components. Communication to servo is modbus so any modbus analyzer would work similarly

Is posibl without setting from pc? So one time settig ithe code, wich code i can change?? Also my ipm module is active low, is posible to invert the output pwm HIN and LIN??.

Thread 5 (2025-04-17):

I was try it to make the pcb, butcanot find the curent sensing

artayasa, 2025-04-17:
Hi mate, i was try to make the ocb, and want to try ur code. But i canot find the ic for curent sensing, isposible tochange to acs712?? Same hall sensor right??

Also for the seting up with new motor wich one need to be change?? My motor 220v 2500ppr, also i have motor 109v 20bit encoder ABZ incremental.

And can i use oscilator standar 8mhz?? I see ur oscilatoe more than that right??

Thank u for great project. Now i wass see ur project was suport step/dir on video but not yet change on readme file.

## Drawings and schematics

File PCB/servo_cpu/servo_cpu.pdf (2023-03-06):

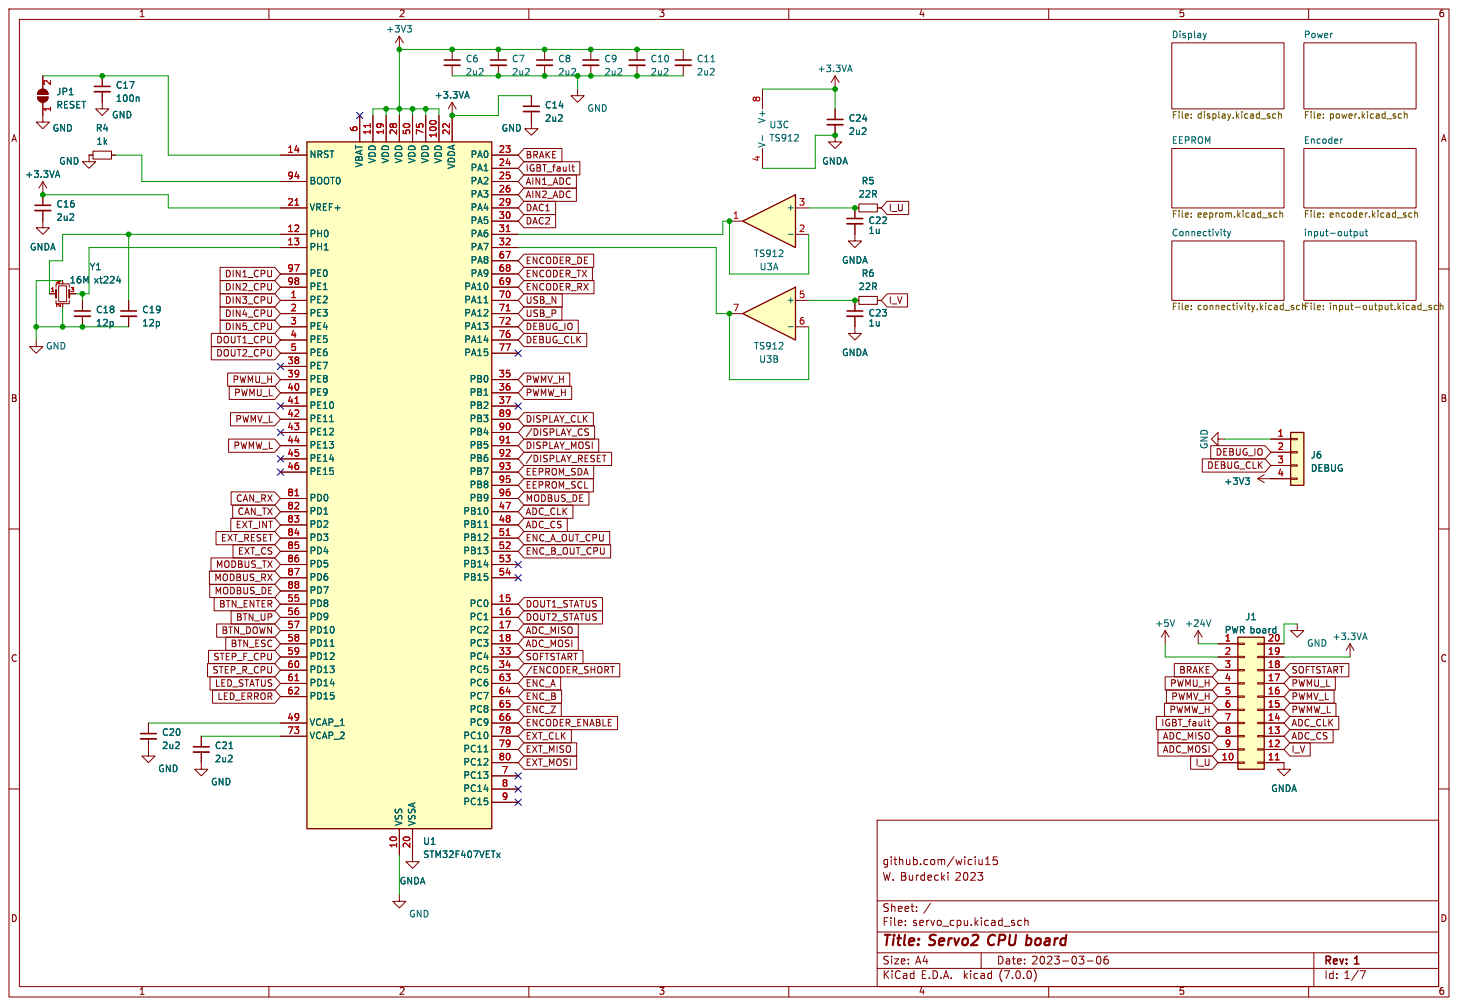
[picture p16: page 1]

input-output File: input-output.kicad_sch

Id: 1/7 Title: Servo2 CPU board

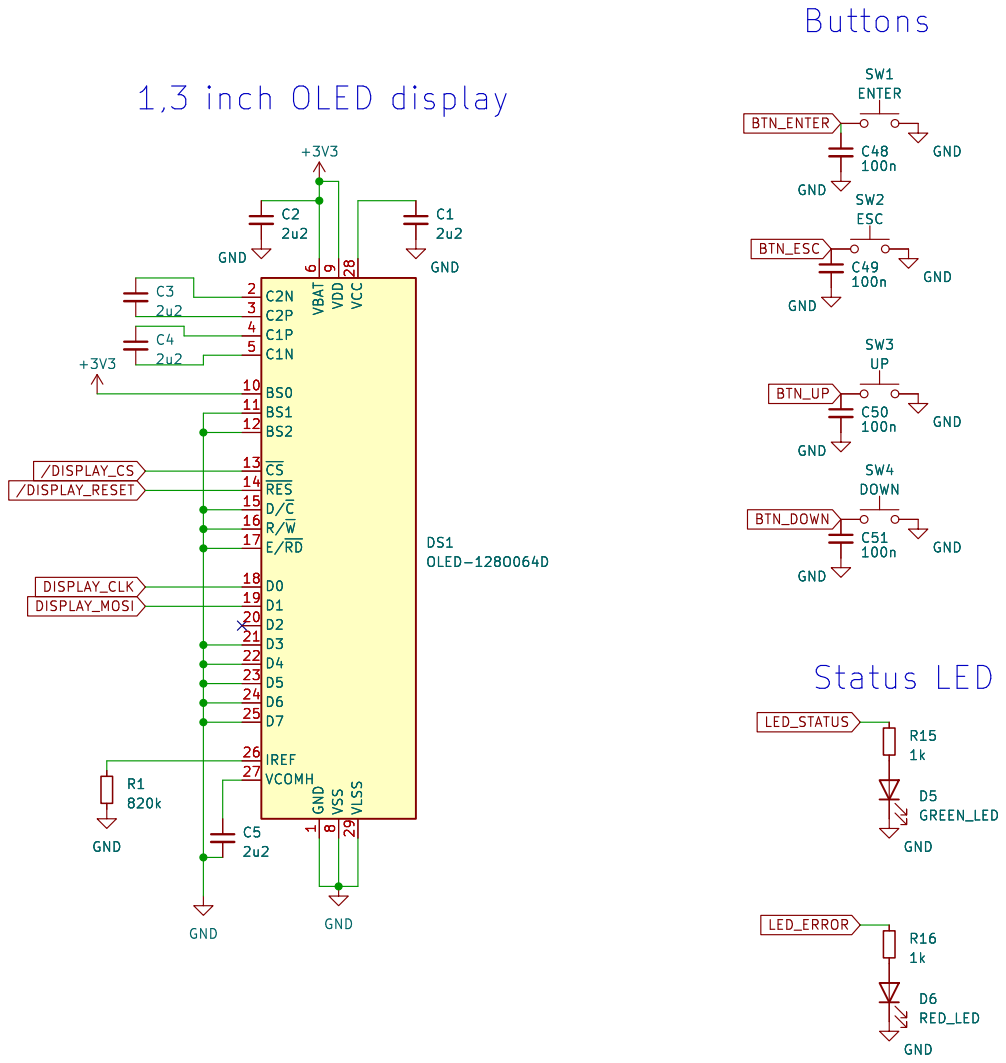
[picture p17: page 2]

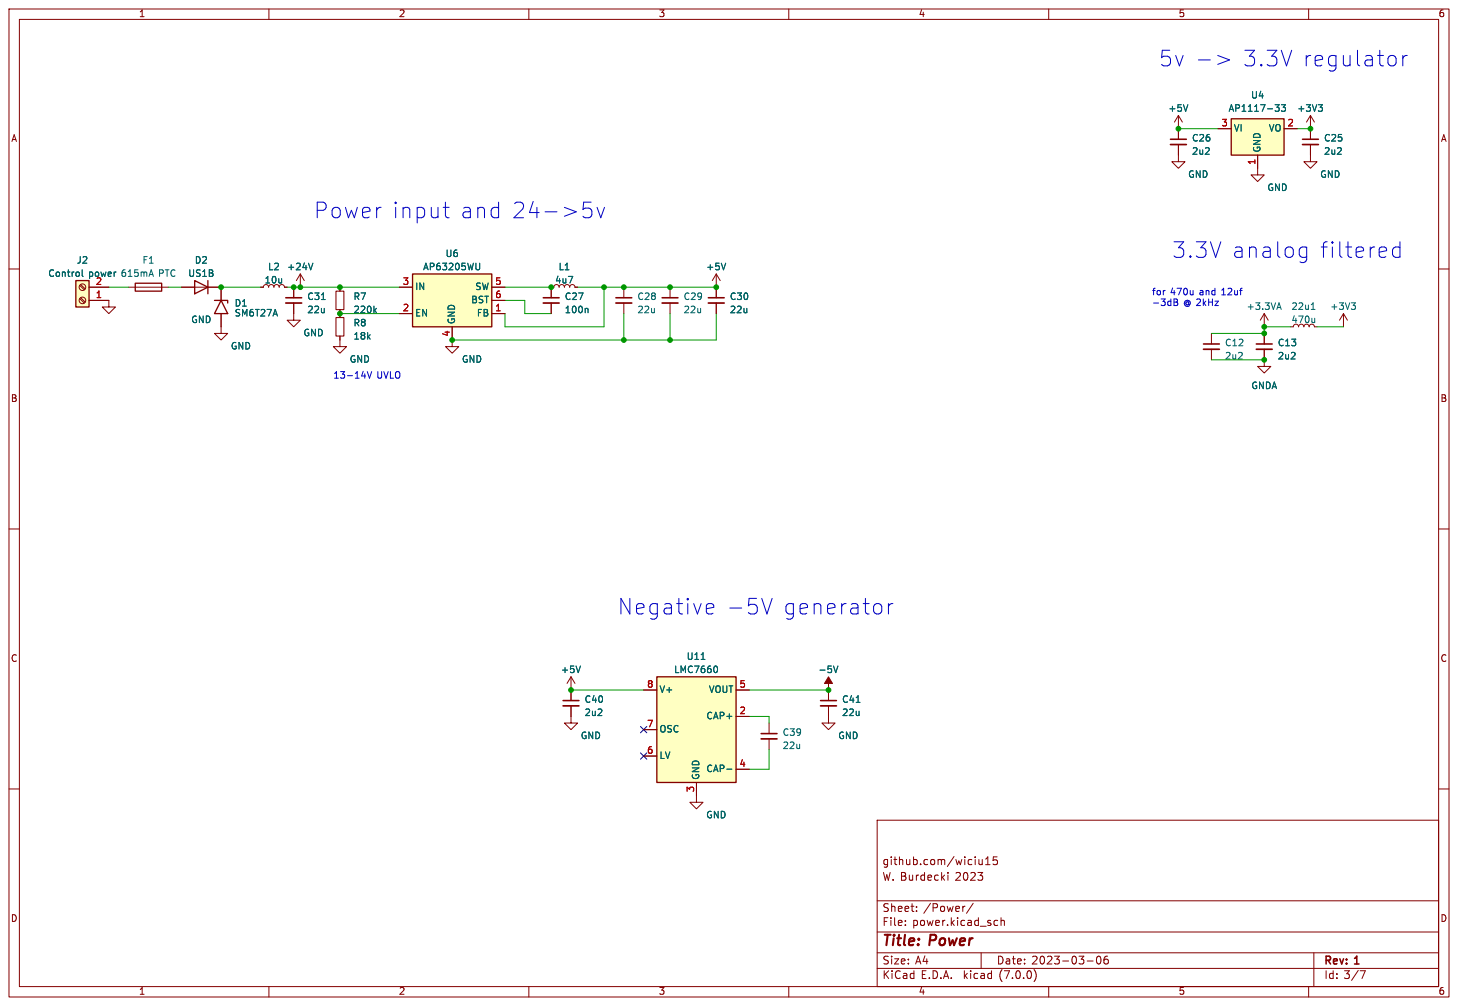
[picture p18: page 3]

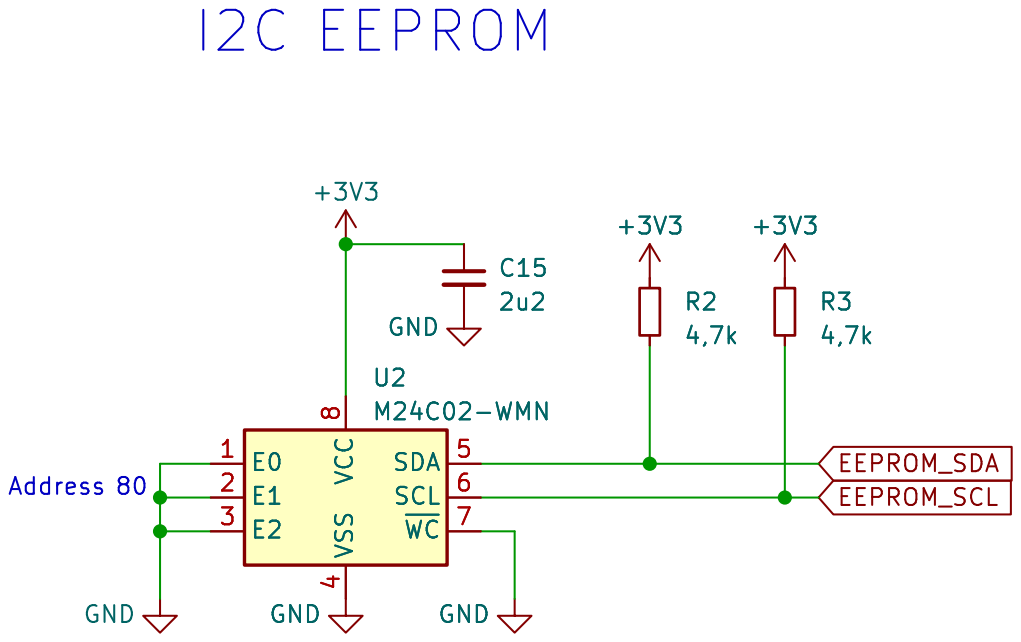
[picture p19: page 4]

4 SDA 5 SCL 6 ~{WC}7 VCC

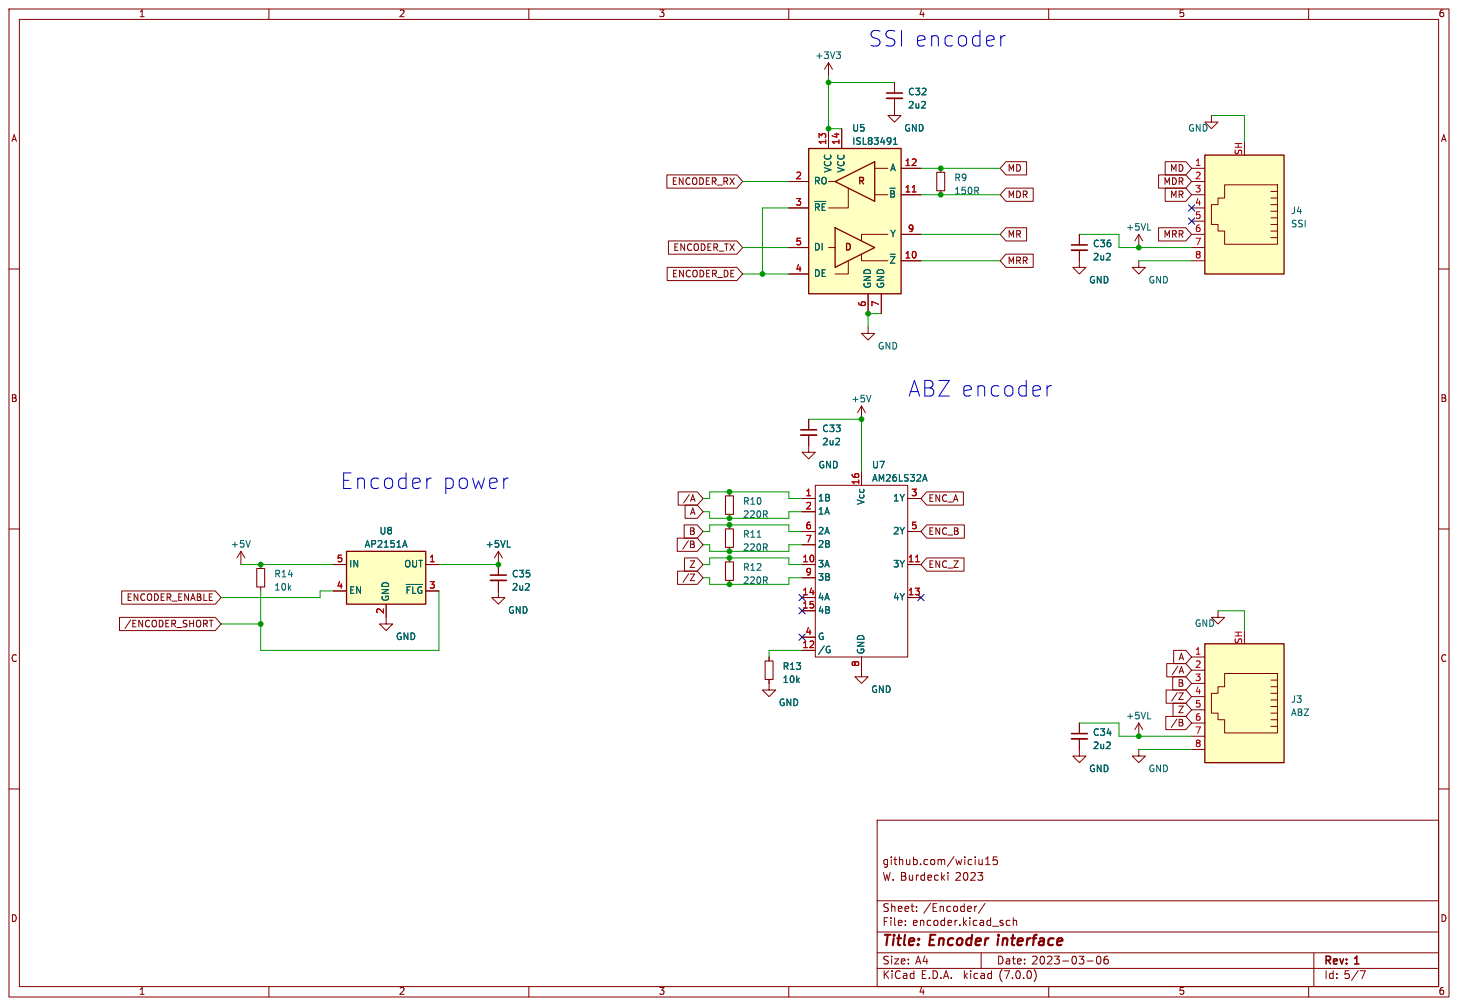
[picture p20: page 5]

Id: 5/7 Title: Encoder interface

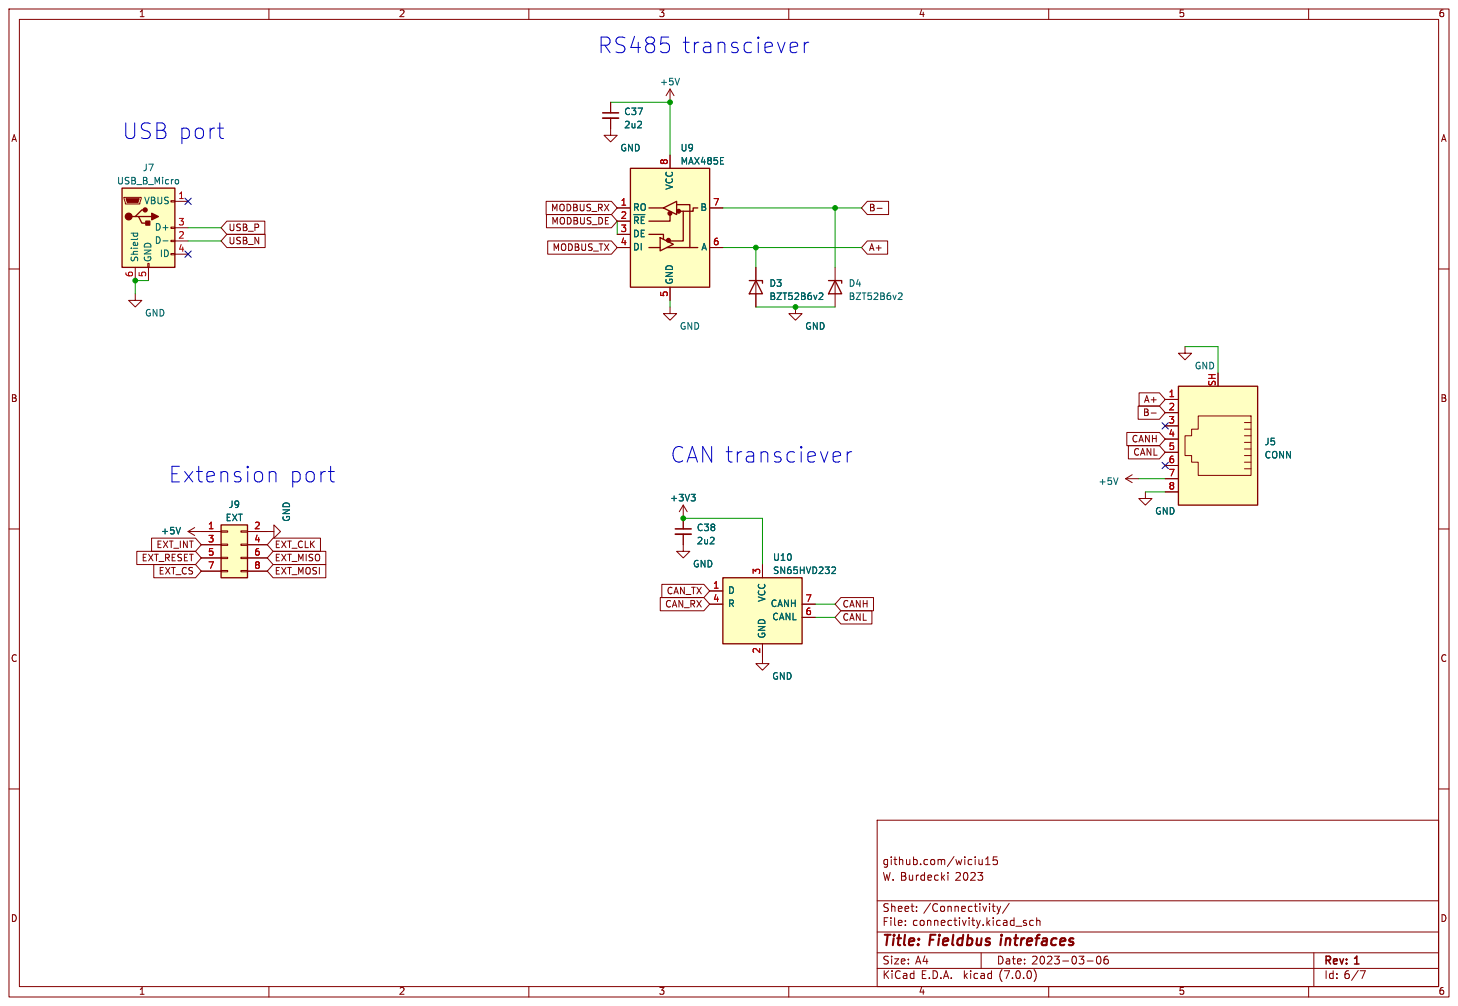
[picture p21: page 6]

Id: 6/7 Title: Fieldbus intrefaces

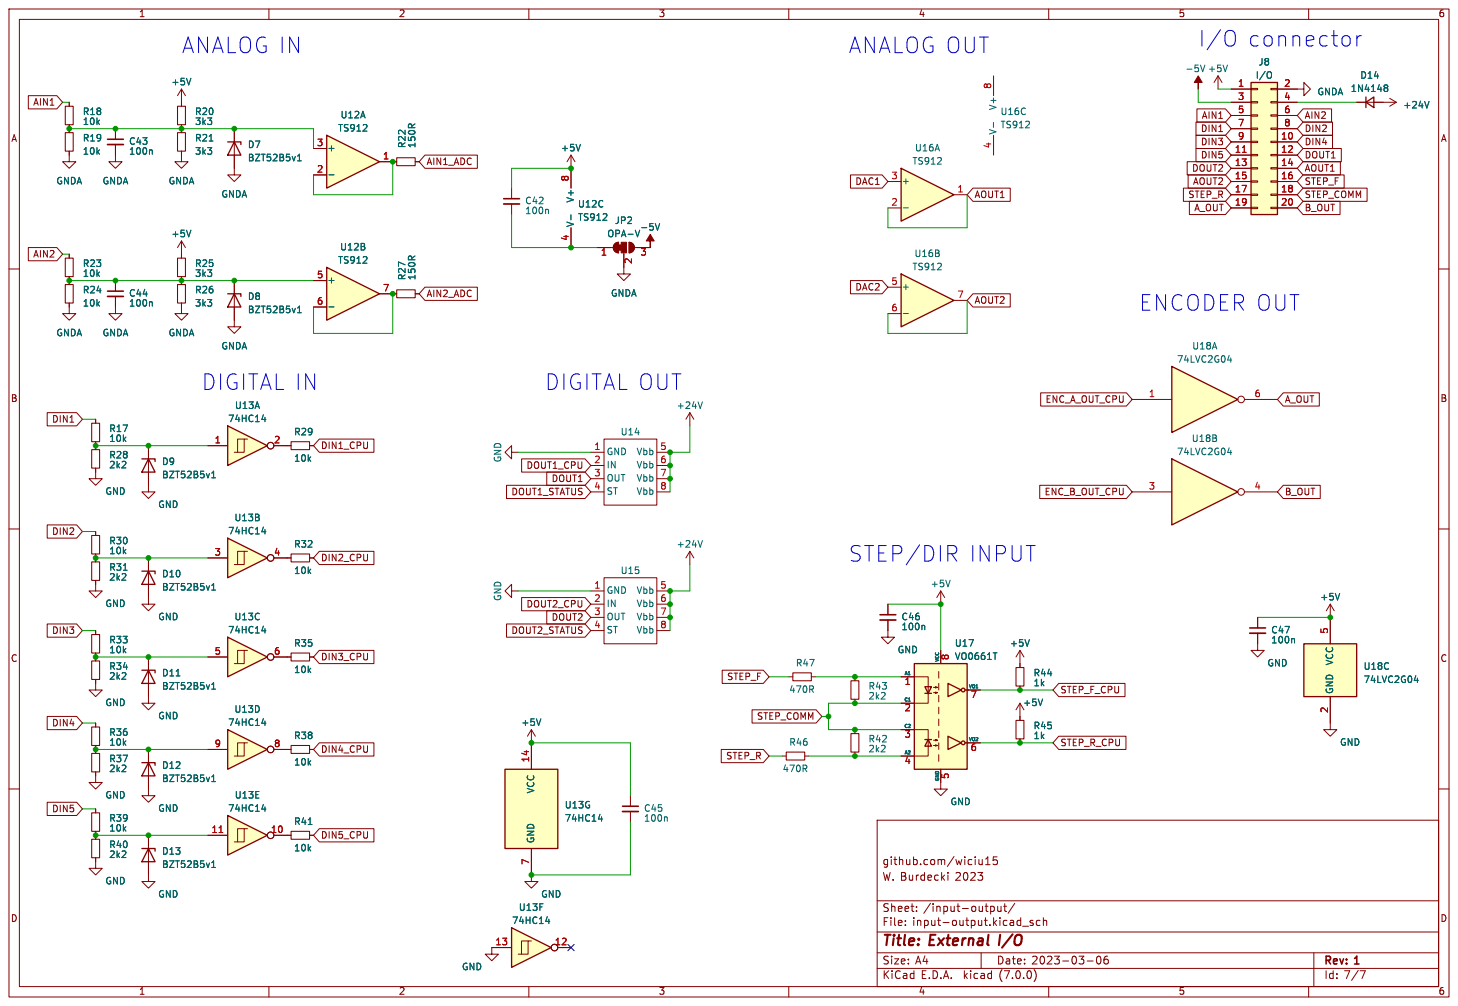
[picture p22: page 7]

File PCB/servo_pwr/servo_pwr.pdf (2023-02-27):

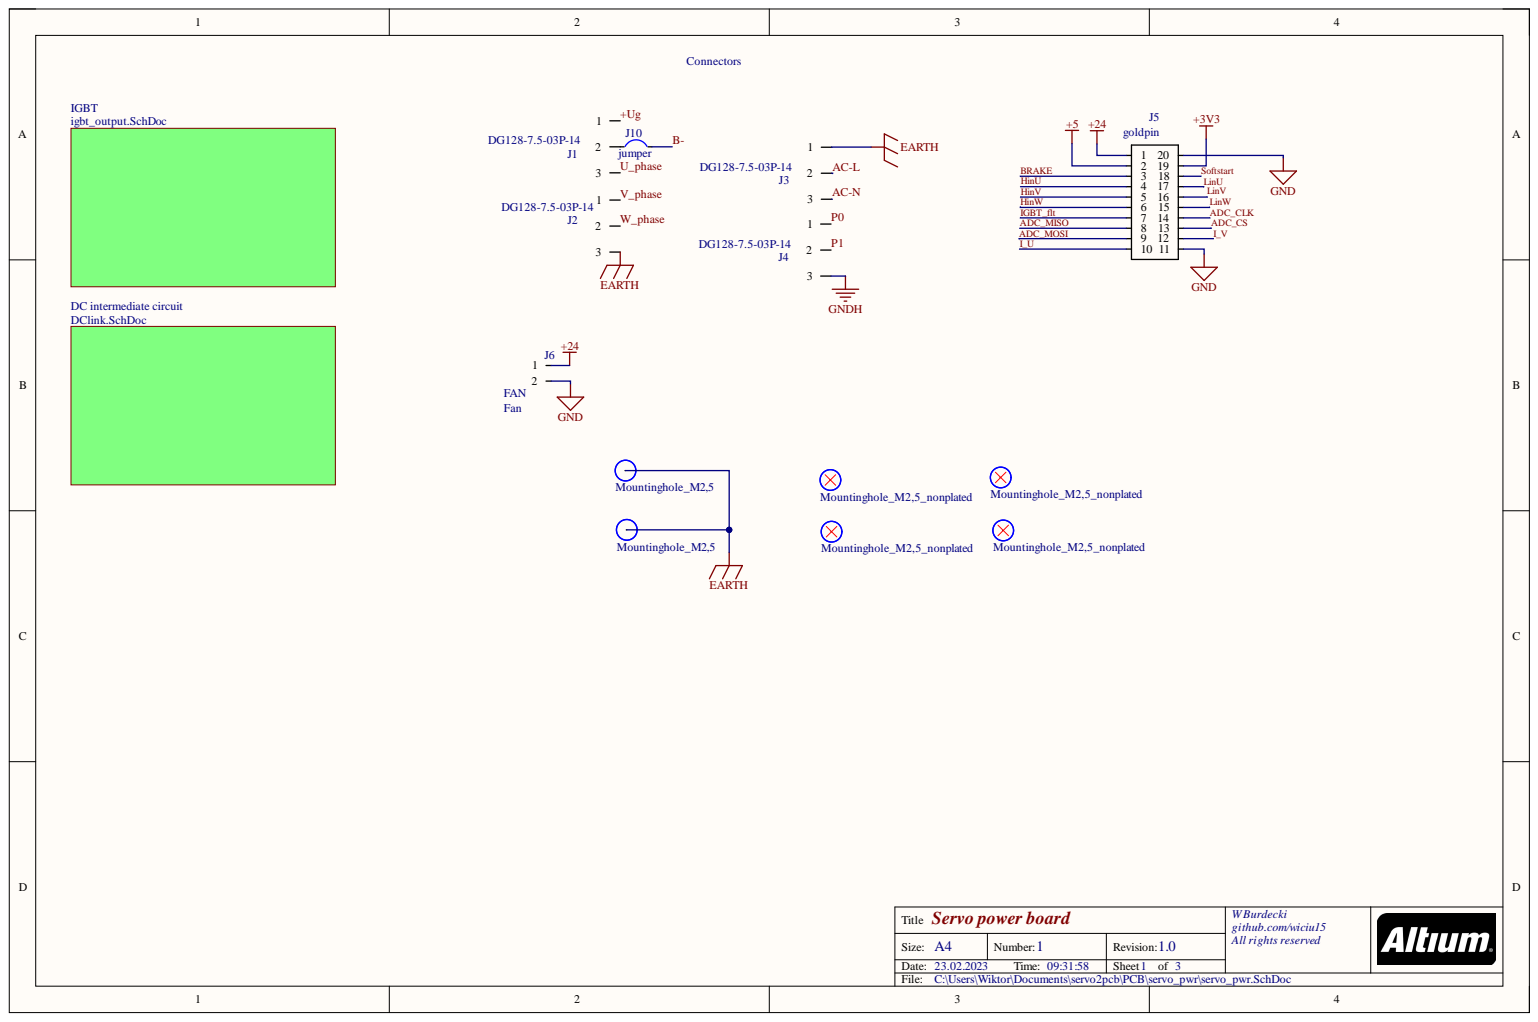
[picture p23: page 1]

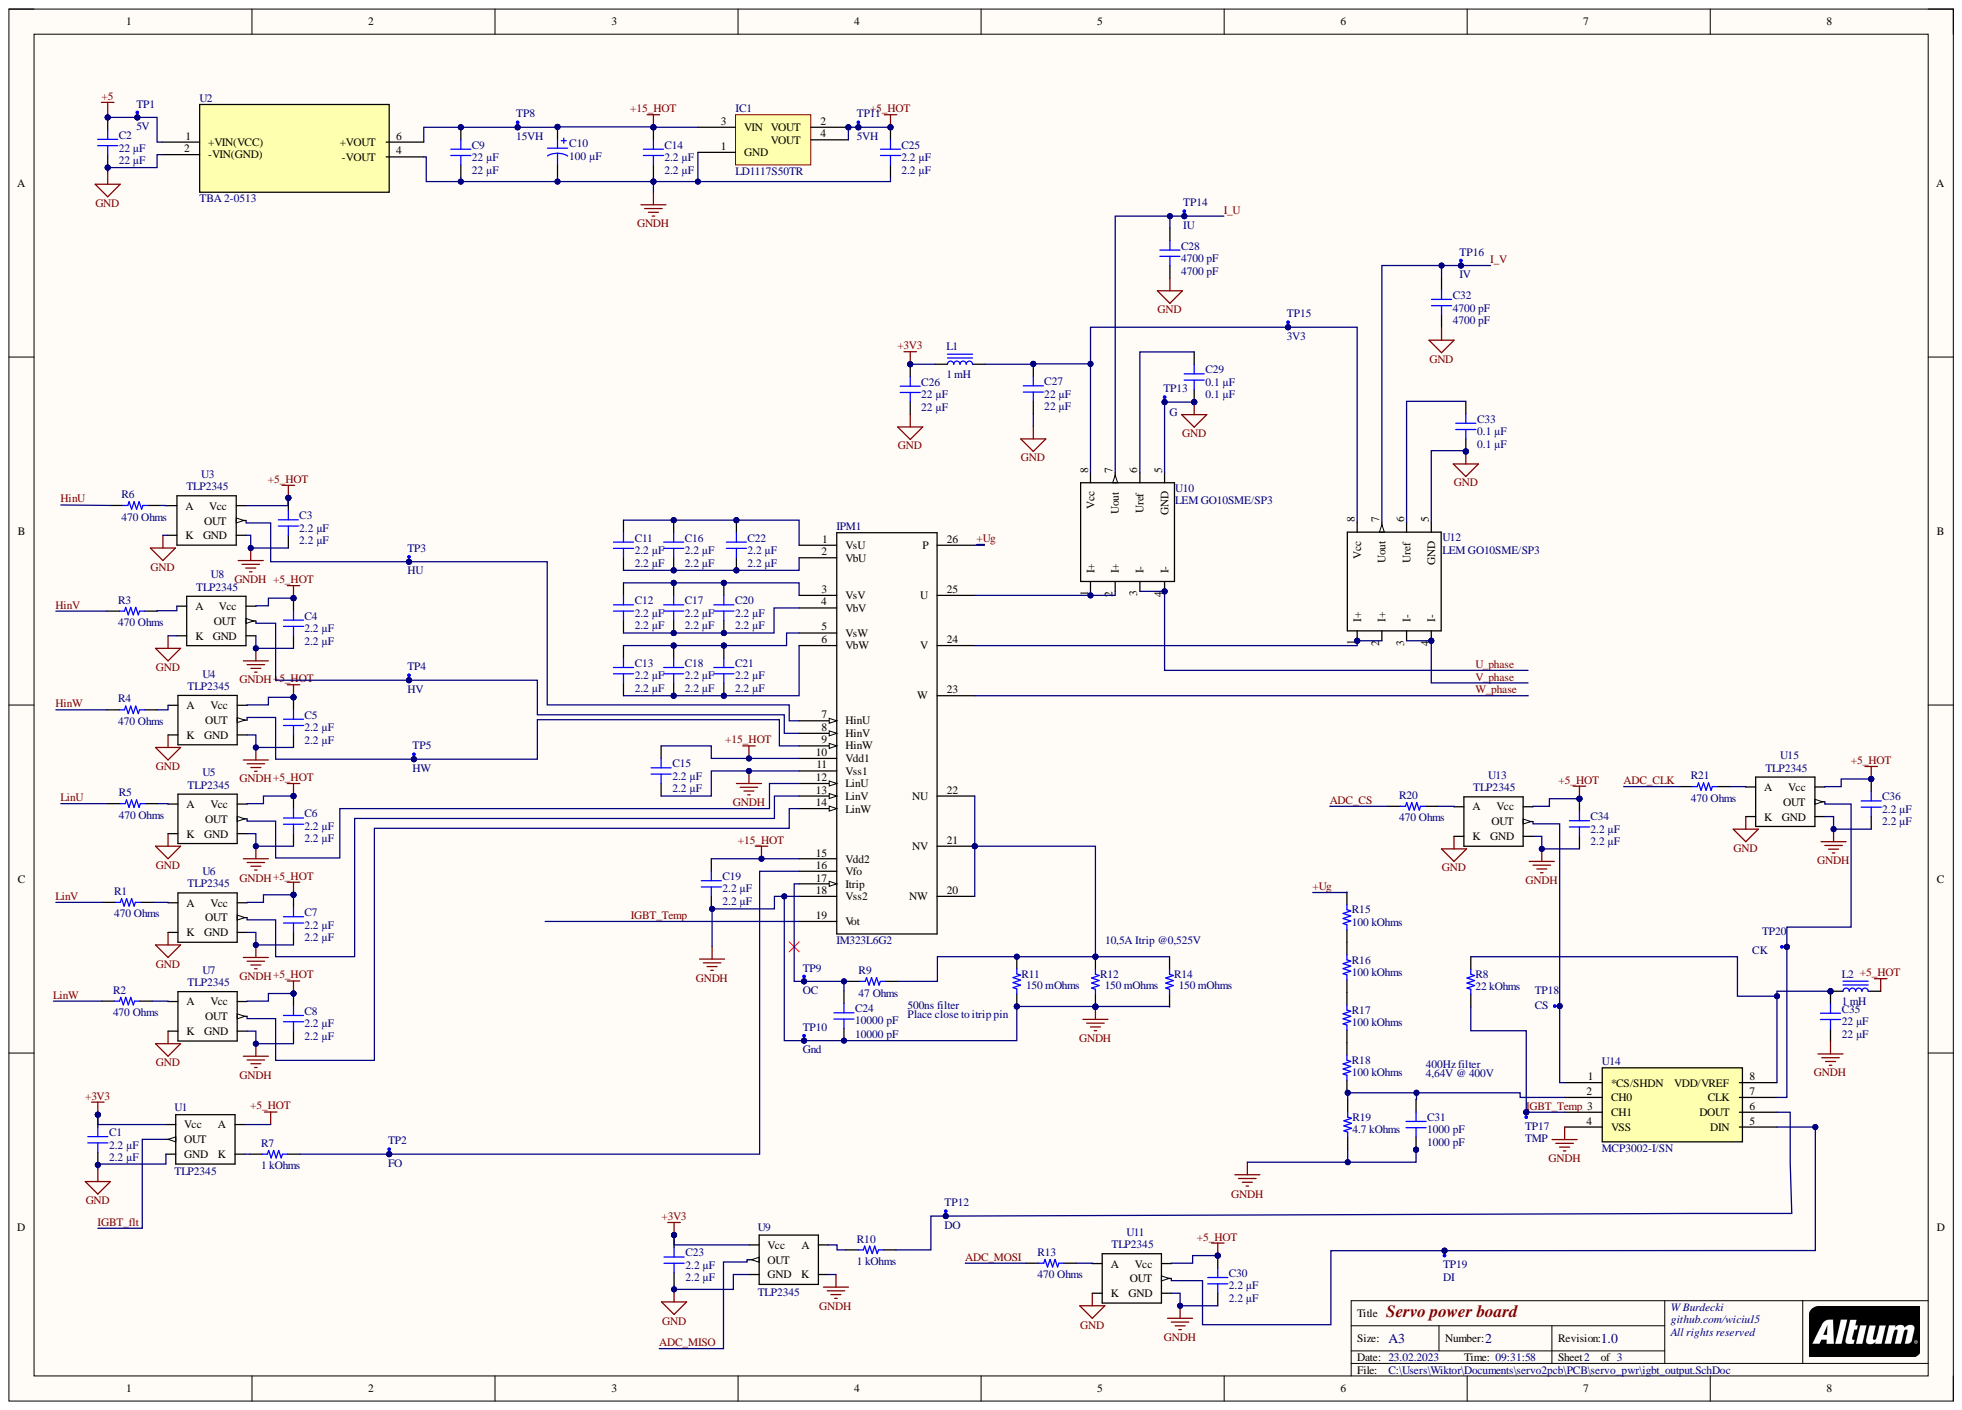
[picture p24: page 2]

+15_HOT | HinV 8

Vdd1 10
Vss1 11

500ns filter Place close to itrip pin

2.2 µF
2.2 µF | +3V3

C:\Users\Wiktor\Documents\servo2pcb\PCB\servo_pwr\igbt_output.SchDoc

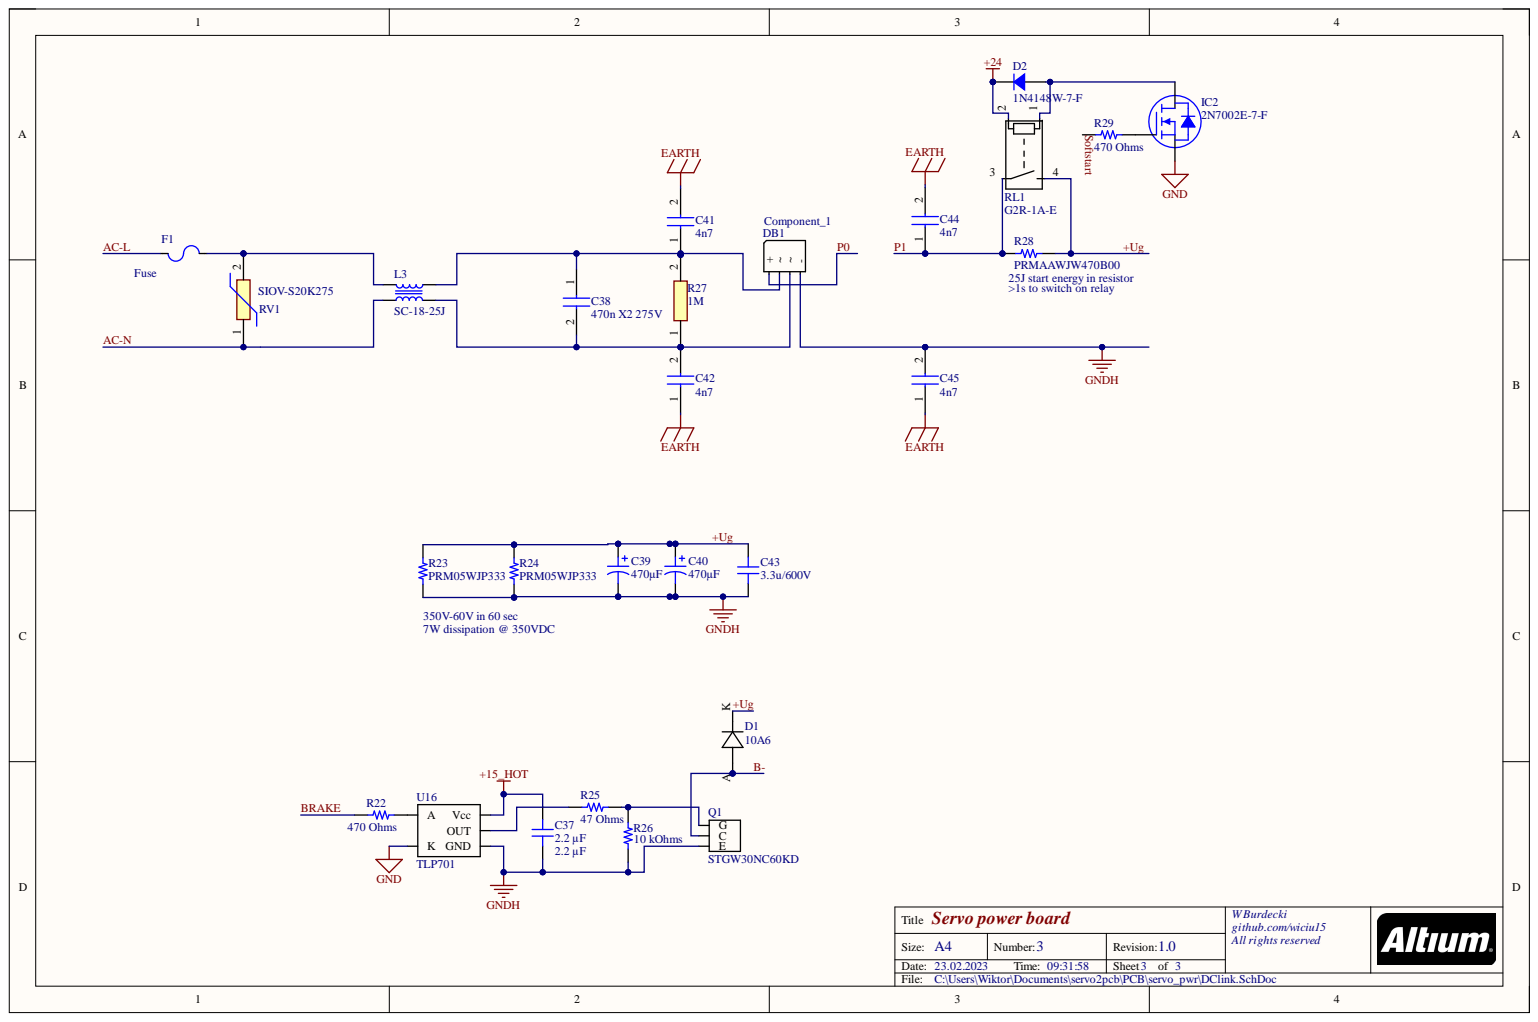
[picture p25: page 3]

PRMAAWJW470B00
25J start energy in resistor >1s to switch on relay

C:\Users\Wiktor\Documents\servo2pcb\PCB\servo_pwr\DClink.SchDoc

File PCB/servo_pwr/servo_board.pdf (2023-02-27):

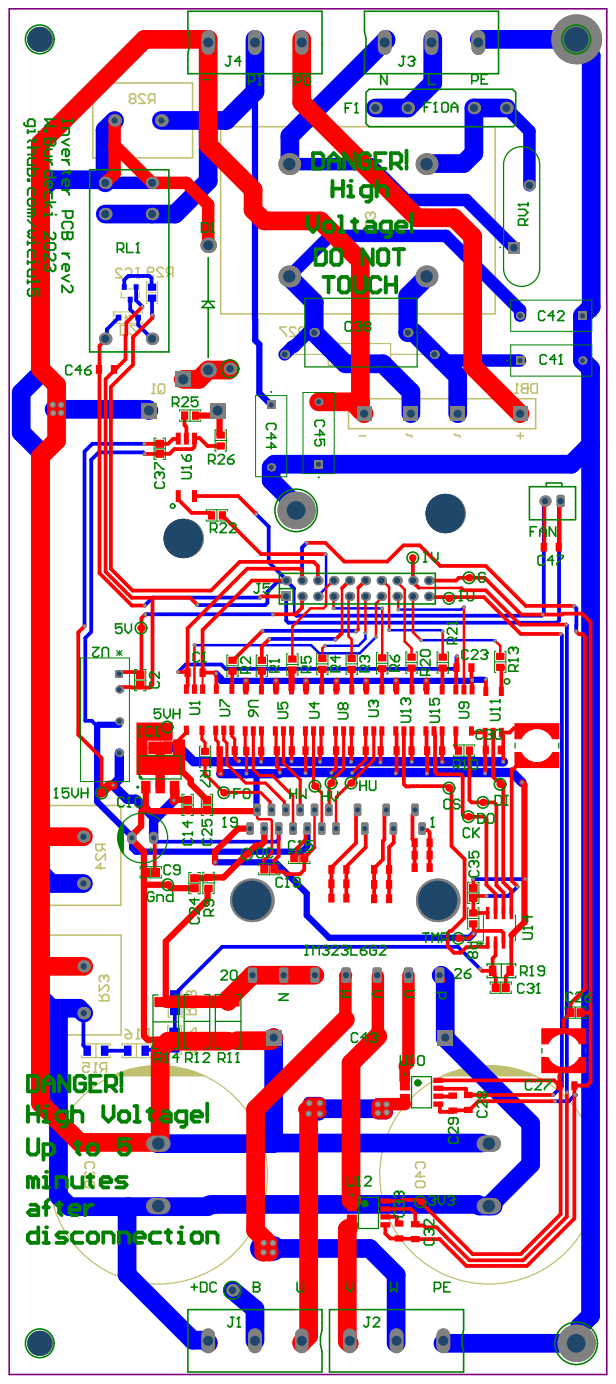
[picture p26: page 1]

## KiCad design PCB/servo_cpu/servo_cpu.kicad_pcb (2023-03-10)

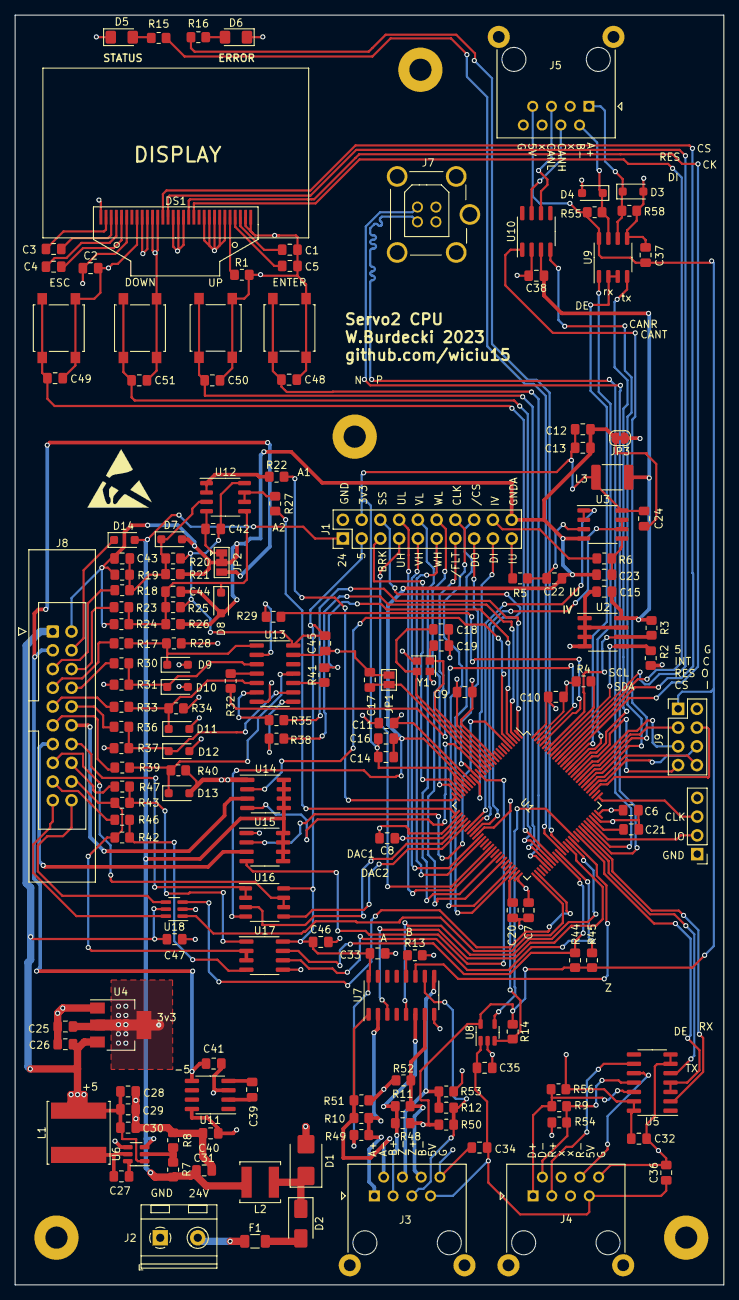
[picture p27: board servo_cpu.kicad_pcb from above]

Board: 4 copper layers, 96.0 x 172.0 mm, 166 parts (0 on the bottom side), 151 nets.

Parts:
C1, C2, C3, C4, C5, C6, C7, C8, C9, C10, C11, C12, C13, C14, C15, C16, C20, C21, C24, C25, C26, C32, C33, C34, C35, C36, C37, C38, C40: 2u2; C_0805_2012Metric_Pad1.18x1.45mm_HandSolder
C17, C27, C42, C43, C44, C45, C46, C47, C48, C49, C50, C51: 100n; C_0805_2012Metric_Pad1.18x1.45mm_HandSolder
C18, C19: 12p; C_0805_2012Metric_Pad1.18x1.45mm_HandSolder
C22, C23: 1u; C_0805_2012Metric_Pad1.18x1.45mm_HandSolder
C28, C29, C30, C31, C39, C41: 22u; C_0805_2012Metric_Pad1.18x1.45mm_HandSolder
D1: SM6T27A; D_SMB
D2: US1B; D_SMA
D3, D4: BZT52B6v2; D_SOD-123F
D5: GREEN_LED; D_1206_3216Metric_Pad1.42x1.75mm_HandSolder
D6: RED_LED; D_1206_3216Metric_Pad1.42x1.75mm_HandSolder
D7, D8, D9, D10, D11, D12, D13: BZT52B5v1; D_SOD-123F
D14: 1N4148; D_SOD-123F
DS1: OLED-128O064D
F1: 615mA PTC; Fuse_1206_3216Metric
J1: PWR board; PinHeader_2x10_P2.54mm_Vertical
J2: Control power; TerminalBlock_RND_205-00232_1x02_P5.08mm_Horizontal
J3: ABZ; RJ45_Ninigi_GE
J4: Serial Encoder; RJ45_Ninigi_GE
J5: CONN; RJ45_Ninigi_GE
J6: DEBUG; PinHeader_1x04_P2.54mm_Vertical
J7: USB_B; USB
J8: I/O; IDC-Header_2x10_P2.54mm_Latch_Vertical
J9: EXT; PinHeader_2x04_P2.54mm_Vertical
JP1: RESET; SolderJumper-2_P1.3mm_Open_Pad1.0x1.5mm
JP2: OPA-V; SolderJumper-3_P1.3mm_Bridged12_Pad1.0x1.5mm
JP3: GND; SolderJumper-2_P1.3mm_Bridged_RoundedPad1.0x1.5mm
L1: 4u7; L_Sunlord_SWPA8040S
L2: 10u; L_Sunlord_SWPA5040S
L3: 470u; L_1812_4532Metric_Pad1.30x3.40mm_HandSolder
MH1, MH1#2, MH1#3, MH1#4: MountingHole_2.7mm_M2.5_DIN965_Pad
R1: 820k; R_0805_2012Metric_Pad1.20x1.40mm_HandSolder
R2, R3: 4,7k; R_0805_2012Metric_Pad1.20x1.40mm_HandSolder
R4, R15, R16, R44, R45, R55: 1k; R_0805_2012Metric_Pad1.20x1.40mm_HandSolder
R5, R6: 22R; R_0805_2012Metric_Pad1.20x1.40mm_HandSolder
R7: 220k; R_0805_2012Metric_Pad1.20x1.40mm_HandSolder
R8: 18k; R_0805_2012Metric_Pad1.20x1.40mm_HandSolder
R9, R22, R27: 150R; R_0805_2012Metric_Pad1.20x1.40mm_HandSolder
R10, R11, R12: 220R; R_0805_2012Metric_Pad1.20x1.40mm_HandSolder
R13, R14, R17, R18, R19, R23, R24, R29, R30, R32, R33, R35, R36, R38, R39, R41: 10k; R_0805_2012Metric_Pad1.20x1.40mm_HandSolder
R20, R21, R25, R26: 3k3; R_0805_2012Metric_Pad1.20x1.40mm_HandSolder
R28, R31, R34, R37, R40, R42, R43: 2k2; R_0805_2012Metric_Pad1.20x1.40mm_HandSolder
R46, R47, R48, R49, R50, R51, R52, R53, R54, R56, R58: 470R; R_0805_2012Metric_Pad1.20x1.40mm_HandSolder
SW1: ENTER; SW_SPST_B3S-1000
SW2: ESC; SW_SPST_B3S-1000
SW3: UP; SW_SPST_B3S-1000
SW4: DOWN; SW_SPST_B3S-1000
U1: STM32F407VETx; LQFP-100_14x14mm_P0.5mm
U2: M24C02-WMN; SOIC-8_3.9x4.9mm_P1.27mm
U3, U12, U16: TS912; SO-8_3.9x4.9mm_P1.27mm
U4: AP1117-33; SOT-223-3_TabPin2
U5: ISL83491; SO-14_3.9x8.65mm_P1.27mm
U6: AP63205WU; TSOT-23-6
U7: AM26LS32A; SO-16_3.9x9.9mm_P1.27mm
U8: AP2151A; SOT-23-5
U9: MAX485E; SO-8_3.9x4.9mm_P1.27mm
U10: SN65HVD232; SOIC-8_3.9x4.9mm_P1.27mm
U11: LMC7660; SOIC-8_3.9x4.9mm_P1.27mm
U13: 74HC14; SO-14_3.9x8.65mm_P1.27mm
U14, U15: ISP742RI; SOIC-8_3.9x4.9mm_P1.27mm
U17: VO0661T; SOIC-8_3.9x4.9mm_P1.27mm
U18: 74LVC2G04; SC-74-6_1.5x2.9mm_P0.95mm
Y1: 16M xt224; Crystal_SMD_2520-4Pin_2.5x2.0mm

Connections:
+3.3VA: C12.1, C13.1, C14.1, C16.1, C24.1, J1.19, L3.1, U1.21 (VREF+), U1.22 (VDDA), U3.8 (V+)
+3V3: C2.1, C6.1, C7.1, C8.1, C9.1, C10.1, C11.1, C15.1, C25.1, C32.1, C38.1, DS1.6 (VBAT), DS1.9 (VDD), DS1.10 (BS0), J6.4, L3.2, R2.1, R3.1, R56.1, U1.11 (VDD), U1.19 (VDD), U1.28 (VDD), U1.50 (VDD), U1.75 (VDD), U1.100 (VDD), U2.8 (VCC), U4.2 (VO), U5.13 (VCC), U5.14 (VCC), U10.3 (VCC)
+5V: C26.1, C28.1, C29.1, C30.1, C33.1, C37.1, C40.1, C42.1, C45.1, C46.1, C47.1, J1.2, J5.7, J8.1, J9.1, L1.2, R14.1, R20.2, R25.2, R44.2, R45.2, R48.1, R49.1, R50.1, R55.1, U4.3 (VI), U6.1 (FB), U7.16 (Vcc), U8.5 (IN), U9.8 (VCC), U11.8 (V+), U12.8 (V+), U13.14 (VCC), U16.8 (V+), U17.8 (VCC), U18.5 (VCC)
+5VL: C34.1, C35.1, C36.1, J3.7, J4.7, U8.1 (OUT)
+24V: C31.1, D14.2 (A), J1.1, L2.2, R7.1, U6.3 (IN), U14.5 (Vbb), U14.6 (Vbb), U14.7 (Vbb), U14.8 (Vbb), U15.5 (Vbb), U15.6 (Vbb), U15.7 (Vbb), U15.8 (Vbb)
-5V: C41.1, J8.3, JP2.3 (B), U11.5 (VOUT)
A: J3.1, R10.2, R49.2, U7.2 (1A)
A+: D3.1 (K), J5.1, R58.1, U9.6 (A)
ADC_CLK: J1.14, U1.47 (PB10)
ADC_CS: J1.13, U1.48 (PB11)
ADC_MISO: J1.8, U1.17 (PC2)
ADC_MOSI: J1.9, U1.18 (PC3)
AIN1: J8.5, R18.2
AIN1_ADC: R22.1, U1.25 (PA2)
AIN2: J8.6, R23.2
AIN2_ADC: R27.1, U1.26 (PA3)
AOUT1: J8.14, U16.1, U16.2 (-)
AOUT2: J8.15, U16.6 (-), U16.7
A_OUT: J8.19, U18.6
B: J3.3, R11.1, R48.2, U7.6 (2A)
B-: D4.1 (K), J5.2, R55.2, U9.7 (B)
BRAKE: J1.3, U1.23 (PA0)
BTN_DOWN: C51.1, SW4.1, U1.57 (PD10)
BTN_ENTER: C48.1, SW1.1, U1.55 (PD8)
BTN_ESC: C49.1, SW2.1, U1.58 (PD11)
BTN_UP: C50.1, SW3.1, U1.56 (PD9)
B_OUT: J8.20, U18.4
CANH: J5.4, U10.7 (CANH)
CANL: J5.5, U10.6 (CANL)
CAN_RX: U1.81 (PD0), U10.4 (R)
CAN_TX: U1.82 (PD1), U10.1 (D)
DAC1: U1.29 (PA4), U16.3 (+)
DAC2: U1.30 (PA5), U16.5 (+)
DEBUG_CLK: J6.3, U1.76 (PA14)
DEBUG_IO: J6.2, U1.72 (PA13)
DIN1: J8.7, R17.2
DIN1_CPU: R29.2, U1.97 (PE0)
DIN2: J8.8, R30.2
DIN2_CPU: R32.2, U1.98 (PE1)
DIN3: J8.9, R33.2
DIN3_CPU: R35.2, U1.1 (PE2)
DIN4: J8.10, R36.2
DIN4_CPU: R38.2, U1.2 (PE3)
DIN5: J8.11, R39.2
DIN5_CPU: R41.2, U1.3 (PE4)
DISPLAY_CLK: DS1.18 (D0), U1.89 (PB3)
DISPLAY_MOSI: DS1.19 (D1), U1.91 (PB5)
DOUT1: J8.12, U14.3 (OUT)
DOUT1_CPU: U1.4 (PE5), U14.2 (IN)
DOUT1_STATUS: U1.15 (PC0), U14.4 (ST)
DOUT2: J8.13, U15.3 (OUT)
DOUT2_CPU: U1.5 (PE6), U15.2 (IN)
DOUT2_STATUS: U1.16 (PC1), U15.4 (ST)
EEPROM_SCL: R3.2, U1.95 (PB8), U2.6 (SCL)
EEPROM_SDA: R2.2, U1.93 (PB7), U2.5 (SDA)
ENCODER_DE: U1.67 (PA8), U5.3 (~RE), U5.4 (DE)
ENCODER_ENABLE: U1.66 (PC9), U8.4 (EN)
ENCODER_RX: U1.69 (PA10), U5.2 (RO)
ENCODER_TX: U1.68 (PA9), U5.5 (DI)
ENC_A: U1.63 (PC6), U7.3 (1Y)
ENC_A_OUT_CPU: U1.51 (PB12), U18.1
ENC_B: U1.64 (PC7), U7.5 (2Y)
ENC_B_OUT_CPU: U1.52 (PB13), U18.3
ENC_Z: U1.65 (PC8), U7.11 (3Y)
EXT_CLK: J9.4, U1.78 (PC10)
EXT_CS: J9.7, U1.85 (PD4)
EXT_INT: J9.3, U1.83 (PD2)
EXT_MISO: J9.6, U1.79 (PC11)
EXT_MOSI: J9.8, U1.80 (PC12)
EXT_RESET: J9.5, U1.84 (PD3)
GND: C1.2, C2.2, C5.2, C6.2, C7.2, C8.2, C9.2, C10.2, C11.2, C15.2, C17.2, C18.2, C19.2, C20.2, C21.2, C25.2, C26.2, C28.2, C29.2, C30.2, C31.2, C32.2, C33.2, C34.2, C35.2, C36.2, C37.2, C38.2, C40.2, C41.2, C45.2, C46.2, C47.2, C48.2, C49.2, C50.2, C51.2, D1.2 (A2), D3.2 (A), D4.2 (A), D5.1 (K), D6.1 (K), D9.2 (A), D10.2 (A), D11.2 (A), D12.2 (A), D13.2 (A), DS1.1 (GND), DS1.8 (VSS), DS1.11 (BS1), DS1.12 (BS2), DS1.15 (D/~C), DS1.16 (R/~W), DS1.17 (E/~RD), DS1.21 (D3), DS1.22 (D4), DS1.23 (D5), DS1.24 (D6), DS1.25 (D7), DS1.29 (VLSS), DS1.30 (GND), J1.20, J2.1, J3.8, J3.SH, J4.8, J4.SH, J5.8, J5.SH, J6.1, J7.4 (GND), J7.5 (Shield), J9.2, JP1.1 (A), JP3.1 (A), MH1.1, MH1#2.1, MH1#3.1, MH1#4.1, R1.2, R4.1, R8.2, R13.2, R28.1, R31.1, R34.1, R37.1, R40.1, R51.2, R52.2, R53.2, R54.2, R58.2, SW1.2, SW2.2, SW3.2, SW4.2, U1.10 (VSS), U1.27 (VSS), U1.74 (VSS), U1.99 (VSS), U2.1 (E0), U2.2 (E1), U2.3 (E2), U2.4 (VSS), U2.7 (~WC), U4.1 (GND), U5.6 (GND), U5.7 (GND), U6.4 (GND), U7.8 (GND), U8.2 (GND), U9.5 (GND), U10.2 (GND), U11.3 (GND), U13.7 (GND), U13.13, U14.1 (GND), U15.1 (GND), U17.5 (GND), U18.2 (GND), Y1.2, Y1.4
GNDA: C12.2, C13.2, C14.2, C16.2, C22.2, C23.2, C24.2, C43.2, C44.2, D7.2 (A), D8.2 (A), J1.11, J8.2, JP2.2 (C), JP3.2 (B), R19.1, R21.1, R24.1, R26.1, U1.20 (VSSA), U3.4 (V-), U16.4 (V-)
IGBT_fault: J1.7, U1.24 (PA1)
I_U: J1.10, R5.2
I_V: J1.12, R6.2
LED_ERROR: R16.1, U1.62 (PD15)
LED_STATUS: R15.1, U1.61 (PD14)
MD: J4.1, R9.1, R56.2, U5.12 (A)
MDR: J4.2, R9.2, R54.1, U5.11 (~B)
MODBUS_DE: U1.88 (PD7), U9.2 (~RE), U9.3 (DE)
MODBUS_RX: U1.87 (PD6), U9.1 (RO)
MODBUS_TX: U1.86 (PD5), U9.4 (DI)
MR: J4.3, U5.9 (Y)
MRR: J4.6, U5.10 (~Z)
unnamed: D1.1 (A1), D2.1 (K), L2.1
unnamed: D2.2 (A), F1.2
unnamed: D5.2 (A), R15.2
unnamed: D6.2 (A), R16.2
unnamed: C43.1, D7.1 (K), R18.1, R19.2, R20.1, R21.2, U12.3 (+)
unnamed: C44.1, D8.1 (K), R23.1, R24.2, R25.1, R26.2, U12.5 (+)
unnamed: D9.1 (K), R17.1, R28.2, U13.1
unnamed: D10.1 (K), R30.1, R31.2, U13.3
unnamed: D11.1 (K), R33.1, R34.2, U13.5
unnamed: D12.1 (K), R36.1, R37.2, U13.9
unnamed: D13.1 (K), R39.1, R40.2, U13.11
unnamed: D14.1 (K), J8.4
unnamed: C4.2, DS1.5 (C1N)
unnamed: C4.1, DS1.4 (C1P)
unnamed: C3.1, DS1.2 (C2N)
unnamed: C3.2, DS1.3 (C2P)
unnamed: DS1.26 (IREF), R1.1
unnamed: C1.1, DS1.28 (VCC)
unnamed: C5.1, DS1.27 (VCOMH)
unnamed: F1.1, J2.2
unnamed: C17.1, JP1.2 (B), U1.14 (NRST)
unnamed: C42.2, JP2.1 (A), U12.4 (V-)
unnamed: R29.1, U13.2
unnamed: R32.1, U13.4
unnamed: R35.1, U13.6
unnamed: R38.1, U13.8
unnamed: R41.1, U13.10
unnamed: R4.2, U1.94 (BOOT0)
unnamed: U1.31 (PA6), U3.1, U3.2 (-)
unnamed: U1.32 (PA7), U3.6 (-), U3.7
unnamed: C19.1, U1.12 (PH0), Y1.1
unnamed: C18.1, U1.13 (PH1), Y1.3
unnamed: C20.1, U1.49 (VCAP_1)
unnamed: C21.1, U1.73 (VCAP_2)
unnamed: C22.1, R5.1, U3.3 (+)
unnamed: C23.1, R6.1, U3.5 (+)
unnamed: C27.2, U6.6 (BST)
unnamed: R7.2, R8.1, U6.2 (EN)
unnamed: C27.1, L1.1, U6.5 (SW)
unnamed: R13.1, U7.12 (/G)
unnamed: C39.1, U11.2 (CAP+)
unnamed: C39.2, U11.4 (CAP-)
unnamed: R22.2, U12.1, U12.2 (-)
unnamed: R27.2, U12.6 (-), U12.7
unnamed: R43.2, R47.2, U17.1 (A1)
unnamed: R42.1, R46.2, U17.4 (A2)
PWMU_H: J1.4, U1.39 (PE8)
PWMU_L: J1.17, U1.40 (PE9)
PWMV_H: J1.5, U1.35 (PB0)
PWMV_L: J1.16, U1.42 (PE11)
PWMW_H: J1.6, U1.36 (PB1)
PWMW_L: J1.15, U1.44 (PE13)
SOFTSTART: J1.18, U1.33 (PC4)
STEP_COMM: J8.18, R42.2, R43.1, U17.2 (C1), U17.3 (C2)
STEP_F: J8.16, R47.1
STEP_F_CPU: R44.1, U1.59 (PD12), U17.7 (VO1)
STEP_R: J8.17, R46.1
STEP_R_CPU: R45.1, U1.60 (PD13), U17.6 (VO2)
USB_N: J7.2 (D-), U1.70 (PA11)
USB_P: J7.3 (D+), U1.71 (PA12)
Z: J3.5, R12.1, R50.2, U7.10 (3A)
/A: J3.2, R10.1, R51.1, U7.1 (1B)
/B: J3.6, R11.2, R52.1, U7.7 (2B)
/DISPLAY_CS: DS1.13 (~CS), U1.90 (PB4)
/DISPLAY_RESET: DS1.14 (~RES), U1.92 (PB6)
/ENCODER_SHORT: R14.2, U1.34 (PC5), U8.3 (~FLG)
/Z: J3.4, R12.2, R53.1, U7.9 (3B)

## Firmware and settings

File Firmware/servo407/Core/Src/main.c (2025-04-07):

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
/* Includes ------------------------------------------------------------------*/
#include "main.h"
#include "cmsis_os.h"
#include "usb_device.h"

/* USER CODE BEGIN Includes */
#include "inverter.h"
#include <math.h>
#include "comm_modbus.h"
#include "comm_canopen.h"
#include "user_interface.h"
#include "eeprom.h"
#include "CO_app_STM32.h"
/* USER CODE END Includes */

typedef StaticTask_t osStaticThreadDef_t;
typedef StaticTimer_t osStaticTimerDef_t;
/* USER CODE BEGIN PD */
/* Debug Exception and Monitor Control Register base address */
#define DEMCR                 *((volatile uint32_t*) 0xE000EDFCu)

/* ITM register addresses */
#define ITM_STIMULUS_PORT0    *((volatile uint32_t*) 0xE0000000u)
#define ITM_TRACE_EN          *((volatile uint32_t*) 0xE0000E00u)
/* USER CODE END PD */

ADC_HandleTypeDef hadc1;
ADC_HandleTypeDef hadc2;
DMA_HandleTypeDef hdma_adc1;
DMA_HandleTypeDef hdma_adc2;

CAN_HandleTypeDef hcan1;

DAC_HandleTypeDef hdac;

I2C_HandleTypeDef hi2c1;
DMA_HandleTypeDef hdma_i2c1_rx;
DMA_HandleTypeDef hdma_i2c1_tx;

SPI_HandleTypeDef hspi1;
SPI_HandleTypeDef hspi2;
SPI_HandleTypeDef hspi3;
DMA_HandleTypeDef hdma_spi1_tx;
DMA_HandleTypeDef hdma_spi2_tx;
DMA_HandleTypeDef hdma_spi2_rx;

TIM_HandleTypeDef htim1;
TIM_HandleTypeDef htim2;
TIM_HandleTypeDef htim3;
TIM_HandleTypeDef htim4;
TIM_HandleTypeDef htim5;
TIM_HandleTypeDef htim6;
TIM_HandleTypeDef htim7;

UART_HandleTypeDef huart1;
UART_HandleTypeDef huart2;
DMA_HandleTypeDef hdma_usart1_rx;
DMA_HandleTypeDef hdma_usart1_tx;

/* Definitions for defaultTask */
osThreadId_t defaultTaskHandle;
const osThreadAttr_t defaultTask_attributes = {
  .name = "defaultTask",
  .stack_size = 256 * 4,
  .priority = (osPriority_t) osPriorityAboveNormal,
};
/* Definitions for taskModbusUSB */
osThreadId_t taskModbusUSBHandle;
const osThreadAttr_t taskModbusUSB_attributes = {
  .name = "taskModbusUSB",
  .stack_size = 1024 * 4,
  .priority = (osPriority_t) osPriorityNormal,
};
/* Definitions for uiTask */
osThreadId_t uiTaskHandle;
uint32_t uiTaskBuffer[ 1024 ];
osStaticThreadDef_t uiTaskControlBlock;
const osThreadAttr_t uiTask_attributes = {
  .name = "uiTask",
  .cb_mem = &uiTaskControlBlock,
  .cb_size = sizeof(uiTaskControlBlock),
  .stack_mem = &uiTaskBuffer[0],
  .stack_size = sizeof(uiTaskBuffer),
  .priority = (osPriority_t) osPriorityBelowNormal,
};
/* Definitions for canopen */
osThreadId_t canopenHandle;
uint32_t canopenBuffer[ 2048 ];
osStaticThreadDef_t canopenControlBlock;
const osThreadAttr_t canopen_attributes = {
  .name = "canopen",
  .cb_mem = &canopenControlBlock,
  .cb_size = sizeof(canopenControlBlock),
  .stack_mem = &canopenBuffer[0],
  .stack_size = sizeof(canopenBuffer),
  .priority = (osPriority_t) osPriorityNormal1,
};
/* Definitions for timerSoftstart */
osTimerId_t timerSoftstartHandle;
osStaticTimerDef_t timerSoftstartControlBlock;
const osTimerAttr_t timerSoftstart_attributes = {
  .name = "timerSoftstart",
  .cb_mem = &timerSoftstartControlBlock,
  .cb_size = sizeof(timerSoftstartControlBlock),
};
/* Definitions for LEDTimer */
osTimerId_t LEDTimerHandle;
osStaticTimerDef_t LEDTimerControlBlock;
const osTimerAttr_t LEDTimer_attributes = {
  .name = "LEDTimer",
  .cb_mem = &LEDTimerControlBlock,
  .cb_size = sizeof(LEDTimerControlBlock),
};
void SystemClock_Config(void);
static void MX_GPIO_Init(void);
static void MX_DMA_Init(void);
static void MX_ADC1_Init(void);
static void MX_ADC2_Init(void);
static void MX_CAN1_Init(void);
static void MX_DAC_Init(void);
static void MX_SPI1_Init(void);
static void MX_SPI2_Init(void);
static void MX_TIM1_Init(void);
static void MX_TIM3_Init(void);
static void MX_TIM4_Init(void);
static void MX_USART1_UART_Init(void);
static void MX_USART2_UART_Init(void);
static void MX_I2C1_Init(void);
static void MX_SPI3_Init(void);
static void MX_TIM2_Init(void);
static void MX_TIM5_Init(void);
static void MX_TIM6_Init(void);
static void MX_TIM7_Init(void);
void StartDefaultTask(void *argument);
void StartTaskModbusUSB(void *argument);
void uiTaskStart(void *argument);
void canopen_task(void *argument);
void timerSoftstartCallback(void *argument);
void LEDTimerCallback(void *argument);

/**
  * @brief  The application entry point.
  * @retval int
  */
int main(void)
{
  /* MCU Configuration--------------------------------------------------------*/

  /* Reset of all peripherals, Initializes the Flash interface and the Systick. */
  HAL_Init();

  /* Configure the system clock */
  SystemClock_Config();

  /* USER CODE BEGIN SysInit */
  // Enable TRCENA
  DEMCR |= ( 1 << 24);
  // Enable stimulus port 0
  ITM_TRACE_EN |= ( 1 << 0);
  /* USER CODE END SysInit */

  /* Initialize all configured peripherals */
  MX_GPIO_Init();
  MX_DMA_Init();
  MX_ADC1_Init();
  MX_ADC2_Init();
  MX_CAN1_Init();
  MX_DAC_Init();
  MX_SPI1_Init();
  MX_SPI2_Init();
  MX_TIM1_Init();
  MX_TIM3_Init();
  MX_TIM4_Init();
  MX_USART1_UART_Init();
  MX_USART2_UART_Init();
  MX_I2C1_Init();
  MX_SPI3_Init();
  MX_TIM2_Init();
  MX_TIM5_Init();
  MX_TIM6_Init();
  MX_TIM7_Init();
  /* Init scheduler */
  osKernelInitialize();

  /* USER CODE BEGIN RTOS_MUTEX */
  /* add mutexes, ... */
  /* USER CODE END RTOS_MUTEX */

  /* USER CODE BEGIN RTOS_SEMAPHORES */
  /* add semaphores, ... */
  /* USER CODE END RTOS_SEMAPHORES */

  /* Create the timer(s) */
  /* creation of timerSoftstart */
  timerSoftstartHandle = osTimerNew(timerSoftstartCallback, osTimerOnce, NULL, &timerSoftstart_attributes);

  /* creation of LEDTimer */
  LEDTimerHandle = osTimerNew(LEDTimerCallback, osTimerPeriodic, NULL, &LEDTimer_attributes);

  /* USER CODE BEGIN RTOS_TIMERS */
  /* start timers, add new ones, ... */
  /* USER CODE END RTOS_TIMERS */

  /* USER CODE BEGIN RTOS_QUEUES */
  /* add queues, ... */
  /* USER CODE END RTOS_QUEUES */

  /* Create the thread(s) */
  /* creation of defaultTask */
  defaultTaskHandle = osThreadNew(StartDefaultTask, NULL, &defaultTask_attributes);

  /* creation of taskModbusUSB */
  taskModbusUSBHandle = osThreadNew(StartTaskModbusUSB, NULL, &taskModbusUSB_attributes);

  /* creation of uiTask */
  uiTaskHandle = osThreadNew(uiTaskStart, NULL, &uiTask_attributes);

  /* creation of canopen */
  canopenHandle = osThreadNew(canopen_task, NULL, &canopen_attributes);

  /* USER CODE BEGIN RTOS_THREADS */
  /* adddefaultTaskHandle ... */
  /* USER CODE END RTOS_THREADS */

  /* USER CODE BEGIN RTOS_EVENTS */
  /* add events, ... */
  /* USER CODE END RTOS_EVENTS */

  /* Start scheduler */
  osKernelStart();
  /* We should never get here as control is now taken by the scheduler */
  /* Infinite loop */
  /* USER CODE BEGIN WHILE */
  while (1)
  {

    /* USER CODE END WHILE */

    /* USER CODE BEGIN 3 */
  }
  /* USER CODE END 3 */
}

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
/* USER CODE BEGIN 4 */

void _putchar(char character)
{
        ITM_SendChar(character);
}

void HAL_ADC_ConvCpltCallback(ADC_HandleTypeDef* hadc){
	//HAL_GPIO_WritePin(ETH_CS_GPIO_Port, ETH_CS_Pin, 1);
	uint16_t avg_U_samples=0;
	uint16_t avg_V_samples=0;
	//calculate zero-current voltage of current transducers to bias further readings
	if(inverter.zerocurrent_ADC_samples_U==0){
		for(uint8_t i=0;i<10;i+=2){
			avg_U_samples+=inverter.output_current_adc_buffer[i];
			avg_V_samples+=inverter.output_current_adc_buffer[i+1];
		}
		inverter.zerocurrent_ADC_samples_U=avg_U_samples/5;
		inverter.zerocurrent_ADC_samples_V=avg_V_samples/5;
	}else{ //average 5 ADC readings and calculate phase currents
		for(uint8_t i=0;i<10;i+=2){
			avg_U_samples+=inverter.output_current_adc_buffer[i];
			avg_V_samples+=inverter.output_current_adc_buffer[i+1];
		}
		//calculate phase current
		inverter.I_U=LowPassFilterA(0.0001f, 0.0000125f, -((float)avg_U_samples/5.0f-inverter.zerocurrent_ADC_samples_U)/ADC_SAMPLES_PER_AMP, &inverter.I_U);
		inverter.I_V=LowPassFilterA(0.0001f, 0.0000125f,-((float)avg_V_samples/5.0f-inverter.zerocurrent_ADC_samples_V)/ADC_SAMPLES_PER_AMP,&inverter.I_V);
		inverter.I_W=-inverter.I_U-inverter.I_V;
		//motor ovecurrent trip
		float currentlimit=parameter_set.motor_max_current*1.5f;
		if(inverter.I_U>currentlimit || inverter.I_U<(-currentlimit)){inverter_error_trip(motor_overcurrent);}
		if(inverter.I_V>currentlimit || inverter.I_V<(-currentlimit)){inverter_error_trip(motor_overcurrent);}
		if(inverter.I_W>currentlimit || inverter.I_W<(-currentlimit)){inverter_error_trip(motor_overcurrent);}
		//inverter overcurrent trip if motor limit higher than inverter limit
		if(inverter.I_U>INVERTER_OVERCURRENT_TRIP_LEVEL || inverter.I_U<(-INVERTER_OVERCURRENT_TRIP_LEVEL)){inverter_error_trip(inverter_overcurrent);}
		if(inverter.I_V>INVERTER_OVERCURRENT_TRIP_LEVEL || inverter.I_V<(-INVERTER_OVERCURRENT_TRIP_LEVEL)){inverter_error_trip(inverter_overcurrent);}
		if(inverter.I_W>INVERTER_OVERCURRENT_TRIP_LEVEL || inverter.I_W<(-INVERTER_OVERCURRENT_TRIP_LEVEL)){inverter_error_trip(inverter_overcurrent);}
	}
	//calculation takes 2us, aquisition of 5(10) samples takes 12,5us
	//HAL_GPIO_WritePin(ETH_CS_GPIO_Port, ETH_CS_Pin, 0);
}

void HAL_SPI_TxCpltCallback(SPI_HandleTypeDef * hspi){
	if(hspi->Instance==SPI1){
		HAL_GPIO_WritePin(OLED_CS_GPIO_Port, OLED_CS_Pin, 1);
	}
}
void HAL_SPI_TxRxCpltCallback(SPI_HandleTypeDef * hspi){
	if(hspi->Instance==SPI2){
		HOT_ADC_RX_Cplt();
	}
}

void HAL_GPIO_EXTI_Callback(uint16_t GPIO_Pin)
{
  if(GPIO_Pin == GPIO_PIN_13) {
	 if(((DIR_IN_GPIO_Port->IDR) & DIR_IN_Pin) != (uint32_t)GPIO_PIN_RESET){TIM4->CR1&= ~(1 << 4);} //dir input polarity is reversed
	 //HAL_GPIO_ReadPin(DIR_IN_GPIO_Port, DIR_IN_Pin);
	 else{TIM4->CR1|=1<<4;}//change STEP input timer counting direction to downcounting,
  }
}

/* USER CODE END 4 */

/* USER CODE BEGIN Header_StartDefaultTask */
/**
 * @brief  Function implementing the defaultTask thread.
 * @param  argument: Not used
 * @retval None
 */
/* USER CODE END Header_StartDefaultTask */
void StartDefaultTask(void *argument)
{
  /* init code for USB_DEVICE */
  MX_USB_DEVICE_Init();
  /* USER CODE BEGIN 5 */
	osThreadSuspend(taskModbusUSBHandle);//start usb communication task
	inverter_setup();
	osThreadResume(taskModbusUSBHandle);//start usb communication task
	osThreadResume(uiTaskHandle);
	/* Infinite loop */
	for(;;)
	{
		DCBus_voltage_check();
		osDelay(1);
	}
  /* USER CODE END 5 */
}

/* USER CODE BEGIN Header_StartTaskModbusUSB */
/**
 * @brief Function implementing the taskModbusUSB thread.
 * @param argument: Not used
* @retval None
*/
/* USER CODE END Header_StartTaskModbusUSB */
void StartTaskModbusUSB(void *argument)
{
  /* USER CODE BEGIN StartTaskModbusUSB */
	//
	ptrModbusUSBinstance=calloc(1,sizeof(modbus_instance_t));
	ModbusUSB_init(ptrModbusUSBinstance);
  /* Infinite loop */
  for(;;)
  {
	process_modbus_command(ptrModbusUSBinstance);
    ulTaskNotifyTake(pdTRUE, portMAX_DELAY);
  }
  /* USER CODE END StartTaskModbusUSB */
}

/* USER CODE BEGIN Header_uiTaskStart */
/**
 * @brief Function implementing the uiTask thread.
 * @param argument: Not used
 * @retval None
 */
/* USER CODE END Header_uiTaskStart */
void uiTaskStart(void *argument)
{
  /* USER CODE BEGIN uiTaskStart */
	osTimerStart(LEDTimerHandle, 100);
	display_init();
	osThreadSuspend(uiTaskHandle);
	osDelay(2000);
	/* Infinite loop */
	for(;;)
	{
		draw();
	}
  /* USER CODE END uiTaskStart */
}

/* USER CODE BEGIN Header_canopen_task */
/**
* @brief Function implementing the canopen thread.
* @param argument: Not used
* @retval None
*/
/* USER CODE END Header_canopen_task */
void canopen_task(void *argument)
{
  /* USER CODE BEGIN canopen_task */
	CANopenNodeSTM32 canOpenNodeSTM32;
	canOpenNodeSTM32.CANHandle = &hcan1;
	canOpenNodeSTM32.HWInitFunction = MX_CAN1_Init;
	canOpenNodeSTM32.timerHandle = &htim6;
	canOpenNodeSTM32.desiredNodeID = 2;
	canOpenNodeSTM32.baudrate = 250;
	initialize_OD_extensions(); //initialize custom read/write functions of parameter list
	canopen_app_init(&canOpenNodeSTM32);
	/* Infinite loop */
	for(;;)
	{
		canopen_app_process();
		osDelay(1);
	}
  /* USER CODE END canopen_task */
}

/* timerSoftstartCallback function */
void timerSoftstartCallback(void *argument)
{
  /* USER CODE BEGIN timerSoftstartCallback */
	if(inverter.DCbus_voltage>=inverter.undervoltage_limit+10.0f){
		HAL_GPIO_WritePin(SOFTSTART_GPIO_Port, SOFTSTART_Pin, 1);
		inverter.softstart_finished=1;
	}
  /* USER CODE END timerSoftstartCallback */
}

/* LEDTimerCallback function */
void LEDTimerCallback(void *argument)
{
  /* USER CODE BEGIN LEDTimerCallback */
	if(HAL_TIM_Base_GetState(&htim5)==HAL_TIM_STATE_BUSY){
		switch(inverter.state){
		case operation_enabled:  //status on error off
			HAL_GPIO_WritePin(LED_STATUS_GPIO_Port, LED_STATUS_Pin,1);
			HAL_GPIO_WritePin(LED_ERROR_GPIO_Port, LED_ERROR_Pin, 0);
			break;
		case switched_on: case ready_to_switch_on: case quickstop_active: //status blink error off
			HAL_GPIO_TogglePin(LED_STATUS_GPIO_Port, LED_STATUS_Pin);
			HAL_GPIO_WritePin(LED_ERROR_GPIO_Port, LED_ERROR_Pin, 0);
			break;
		case switch_on_disabled: //status off error blink
			HAL_GPIO_WritePin(LED_STATUS_GPIO_Port, LED_STATUS_Pin,0);
			HAL_GPIO_TogglePin(LED_ERROR_GPIO_Port, LED_ERROR_Pin);
			break;
		case faulted: //status off error on
			HAL_GPIO_WritePin(LED_STATUS_GPIO_Port, LED_STATUS_Pin,0);
			HAL_GPIO_WritePin(LED_ERROR_GPIO_Port, LED_ERROR_Pin, 1);
			break;
		default: //both on
			HAL_GPIO_WritePin(LED_STATUS_GPIO_Port, LED_STATUS_Pin, 1);
			HAL_GPIO_WritePin(LED_ERROR_GPIO_Port, LED_ERROR_Pin, 1);
			break;
		}
	}else{
		//both on if motor control loop is not working
		HAL_GPIO_WritePin(LED_STATUS_GPIO_Port, LED_STATUS_Pin, 1);
		HAL_GPIO_WritePin(LED_ERROR_GPIO_Port, LED_ERROR_Pin, 1);
	}
  /* USER CODE END LEDTimerCallback */
}

/**
  * @brief  Period elapsed callback in non blocking mode
  * @note   This function is called  when TIM11 interrupt took place, inside
  * HAL_TIM_IRQHandler(). It makes a direct call to HAL_IncTick() to increment
  * a global variable "uwTick" used as application time base.
  * @param  htim : TIM handle
  * @retval None
  */
void HAL_TIM_PeriodElapsedCallback(TIM_HandleTypeDef *htim)
{
  if (htim->Instance == TIM11) {
    HAL_IncTick();
  }
  /* USER CODE BEGIN Callback 1 */
  if(htim->Instance == TIM6) {
	  canopen_app_interrupt();
  }
  if(htim->Instance == TIM7) {
	  if((parameter_set.motor_feedback_type==mitsubishi_encoder) && (mitsubishi_encoder_data.encoder_state!=encoder_error_no_communication || mitsubishi_encoder_data.encoder_state!=encoder_error_cheksum )){
	  		mitsubishi_encoder_send_command();
	  	}
	  if(parameter_set.motor_feedback_type==delta_encoder){delta_encoder_read_position();}

    }
  /* USER CODE END Callback 1 */
}

/**
  * @brief  This function is executed in case of error occurrence.
  * @retval None
  */
void Error_Handler(void)
{
  /* USER CODE BEGIN Error_Handler_Debug */
  /* User can add his own implementation to report the HAL error return state */
  __disable_irq();
  while (1)
  {
  }
  /* USER CODE END Error_Handler_Debug */
}

#ifdef  USE_FULL_ASSERT
/**
  * @brief  Reports the name of the source file and the source line number
  *         where the assert_param error has occurred.
  * @param  file: pointer to the source file name
  * @param  line: assert_param error line source number
  * @retval None
  */
void assert_failed(uint8_t *file, uint32_t line)
{
  /* USER CODE BEGIN 6 */
  /* User can add his own implementation to report the file name and line number,
     ex: printf("Wrong parameters value: file %s on line %d\r\n", file, line) */
  /* USER CODE END 6 */
}
#endif /* USE_FULL_ASSERT */

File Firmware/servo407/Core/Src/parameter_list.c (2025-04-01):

/*
 * parameter_list.c
 *
 *  Created on: Aug 2, 2023
 *      Author: Wiktor
 */

#include "parameter_list.h"
#include <string.h>
#include <math.h>

HAL_StatusTypeDef limiter(parameter_t * par, void * pValue, void * pReturnValue);
HAL_StatusTypeDef prepare_received_data(parameter_t * par, uint32_t * pReceivedData, void * pReturnValue);

parameter_t parameter_list[]={
		{.number=1,.ModbusAddress=1,.CANAddress=0x606C,.name={"Actual speed"},.shortName={"Act spd"},.description={"Actual motor speed"},.WriteAllowed=0,.precision=0,.unit="RPM",.ModbusDataType=mbINT16,.type=pINT16,.multiplierMB=1.0f,.minValue=-10000.0f,.maxValue=10000.0f,.defaultValue=0.0f},
		{.number=2,.ModbusAddress=2,.CANAddress=1111,.name={"Apparent current"},.shortName={"I mot"},.description={"Actual motor RMS current"},.WriteAllowed=0,.precision=2,.unit="A",.ModbusDataType=mbINT16,.type=pFLOAT,.multiplierMB=0.01f,.minValue=-32000.0f,.maxValue=32000.0f,.defaultValue=0.0f},
		{.number=3,.ModbusAddress=3,.CANAddress=1111,.name={"Magnetizing current"},.shortName={"I mag"},.description={"Magnetizing RMS current"},.WriteAllowed=0,.precision=2,.unit="A",.ModbusDataType=mbINT16,.type=pFLOAT,.multiplierMB=0.01f,.minValue=-32000.0f,.maxValue=32000.0f,.defaultValue=0.0f},
		{.number=4,.ModbusAddress=4,.CANAddress=1111,.name={"Torque current"},.shortName={"I trq"},.description={"Torque-producing RMS current"},.WriteAllowed=0,.precision=2,.unit="A",.ModbusDataType=mbINT16,.type=pFLOAT,.multiplierMB=0.01f,.minValue=-32000.0f,.maxValue=32000.0f,.defaultValue=0.0f},
		{.number=5,.ModbusAddress=5,.CANAddress=1111,.name={"Motor torque"},.shortName={"Mot trq"},.description={"Actaul motor torque in %"},.WriteAllowed=0,.precision=1,.unit="%",.ModbusDataType=mbINT16,.type=pFLOAT,.multiplierMB=0.01f,.minValue=-1000.0f,.maxValue=1000.0f,.defaultValue=0.0f},
		{.number=6,.ModbusAddress=6,.CANAddress=1111,.name={"Actual position L"},.shortName={"Act posL"},.description={"Actual rotor position low word"},.WriteAllowed=0,.precision=0,.unit="",.ModbusDataType=mbINT16,.type=pINT16,.multiplierMB=1.0f,.minValue=-32768.0f,.maxValue=32767.0f,.defaultValue=0.0f},
		{.number=7,.ModbusAddress=7,.CANAddress=0x6064,.name={"Actual position H"},.shortName={"Act posH"},.description={"Actual axis position high word"},.WriteAllowed=0,.precision=0,.unit="",.ModbusDataType=mbINT16,.type=pINT16,.multiplierMB=1.0f,.minValue=-32768.0f,.maxValue=32767.0f,.defaultValue=0.0f},
		{.number=8,.ModbusAddress=8,.CANAddress=1111,.name={"Target position L"},.shortName={"Tht posL"},.description={"Target axis position high word"},.WriteAllowed=1,.precision=0,.unit="",.ModbusDataType=mbINT16,.type=pINT16,.multiplierMB=1.0f,.minValue=-32768.0f,.maxValue=32767.0f,.defaultValue=0.0f},
		{.number=9,.ModbusAddress=9,.CANAddress=1111,.name={"Target position H"},.shortName={"Tgt posH"},.description={"Target axis position high word"},.WriteAllowed=1,.precision=0,.unit="",.ModbusDataType=mbINT16,.type=pINT16,.multiplierMB=1.0f,.minValue=-32768.0f,.maxValue=32767.0f,.defaultValue=0.0f},
		{.number=10,.ModbusAddress=10,.CANAddress=1111,.name={"Motor voltage"},.shortName={"U mot"},.description={"Actual motor RMS voltage"},.WriteAllowed=0,.precision=1,.unit="V",.ModbusDataType=mbUINT16,.type=pFLOAT,.multiplierMB=0.1f,.minValue=0.0f,.maxValue=65535.0f,.defaultValue=0.0f},
		{.number=11,.ModbusAddress=11,.CANAddress=1111,.name={"DC bus voltage"},.shortName={"DC bus"},.description={"Actual voltage in intermediate circuit"},.WriteAllowed=0,.precision=1,.unit="V",.ModbusDataType=mbUINT16,.type=pFLOAT,.multiplierMB=0.1f,.minValue=0.0f,.maxValue=65535.0f,.defaultValue=0.0f},
		{.number=12,.ModbusAddress=12,.CANAddress=1111,.name={"Motor thermal load"},.shortName={"Mot I2t"},.description={"Motor thermal calculated from output current"},.WriteAllowed=0,.precision=1,.unit="%",.ModbusDataType=mbUINT16,.type=pFLOAT,.multiplierMB=0.1f,.minValue=0.0f,.maxValue=65535.0f,.defaultValue=0.0f},
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

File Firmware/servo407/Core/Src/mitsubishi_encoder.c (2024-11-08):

/*
 * mitsubishi_encoder.c
 *
 *  Created on: Jun 7, 2023
 *      Author: Wiktor
 */


#include "mitsubishi_encoder.h"
#include "cmsis_os.h"
#include "inverter.h"
#include <string.h>
#include <math.h>
extern UART_HandleTypeDef huart1;

mitsubishi_encoder_data_t mitsubishi_encoder_data;
HAL_StatusTypeDef status;

//very fast register level UART transmit of 1 byte with RE/DE gpio line support.
HAL_StatusTypeDef USART_fast_transmit_RS485(UART_HandleTypeDef * huart, uint8_t byte_to_send){
	uint32_t timeout_clock=0;
	HAL_GPIO_WritePin(ENCODER_DE_GPIO_Port,ENCODER_DE_Pin, 1);
	huart->Instance->DR=byte_to_send;
	while(!__HAL_UART_GET_FLAG(huart,UART_FLAG_TC)){timeout_clock++;if(timeout_clock>60){break;}} //break out of loop if transfer is not finished within <1us to prevent blocking the CPU in case of error
	ENCODER_DE_GPIO_Port->BSRR = (uint32_t)ENCODER_DE_Pin << 16U;
	if(timeout_clock<60){return HAL_OK;}
	return HAL_ERROR;
}

void mitsubishi_motor_identification(void){
	//first send 4 packets with 0x92 command  (encoder reset probably, then 8 with 0x7A command (motor data read)
	mitsubishi_encoder_data.encoder_command = 0x92;
	for(uint8_t i=0;i<=30;i++){
		if(i>=11){mitsubishi_encoder_data.encoder_command=0x7A;}
		mitsubishi_encoder_send_command();
		osDelay(1);
		if(i>15 && mitsubishi_encoder_data.motor_response[0]==0x7A){break;}
		if(i>=29){mitsubishi_encoder_data.encoder_state=encoder_error_no_communication;}
	}
	//check if encoder sent valid data back by calculating XOR
	memcpy(&mitsubishi_encoder_data.motor_data_response_packet,&mitsubishi_encoder_data.motor_response,9);
	uint8_t xor_cheksum=0;
	for(uint8_t i=0;i<8;i++){
		xor_cheksum^=mitsubishi_encoder_data.motor_data_response_packet[i];
	}
	if(xor_cheksum!=mitsubishi_encoder_data.motor_data_response_packet[8]){
		mitsubishi_encoder_data.encoder_state=encoder_error_cheksum;
	}else{
		if(mitsubishi_encoder_data.motor_data_response_packet[0]==0x7A ){
			//if response is valid decode motor data and encoder resolution
			if(mitsubishi_encoder_data.motor_data_response_packet[2]==0x3D){mitsubishi_encoder_data.encoder_resolution=8192;set_encoder_frequency(2000);mitsubishi_encoder_data.motor_family=j2_13bit;} //j2 encoder
			else if(mitsubishi_encoder_data.motor_data_response_packet[2]==0x3C){mitsubishi_encoder_data.encoder_resolution=16384;mitsubishi_encoder_data.motor_family=j2_14bit;} //j2 encoder
			else if(mitsubishi_encoder_data.motor_data_response_packet[2]==0x41){mitsubishi_encoder_data.encoder_resolution=65535;set_encoder_frequency(16000);mitsubishi_encoder_data.motor_family=j2super;} //j2super 17 bit encoders
			else if(mitsubishi_encoder_data.motor_data_response_packet[2]==0x4B){mitsubishi_encoder_data.encoder_resolution=65535;set_encoder_frequency(16000);mitsubishi_encoder_data.motor_family=je;} //mr-je/mr-e encoder 17bit
			else if(mitsubishi_encoder_data.motor_data_response_packet[2]==0x44){mitsubishi_encoder_data.encoder_resolution=65535;mitsubishi_encoder_data.motor_family=j3j4;} //j3 and j4 encoder have the same encoder id but j4 claims 22bit resolution, maybe different command is needed
			else if(mitsubishi_encoder_data.motor_data_response_packet[2]==0x8F){mitsubishi_encoder_data.encoder_resolution=67108864;set_encoder_frequency(8000);mitsubishi_encoder_data.motor_family=j5;} //very limited support
			else{mitsubishi_encoder_data.encoder_resolution=131072;mitsubishi_encoder_data.motor_family=unknown_family;}
			mitsubishi_encoder_data.motor_series_id=mitsubishi_encoder_data.motor_data_response_packet[3];
			//determine speed and power
			mitsubishi_encoder_data.motor_power=(mitsubishi_encoder_data.motor_data_response_packet[4] >> 4)*100;
			mitsubishi_encoder_data.motor_speed=(mitsubishi_encoder_data.motor_data_response_packet[4] & 0x0F)*1000;
			//set command to send to encoder depending on its type
			if(mitsubishi_encoder_data.encoder_resolution==8192){mitsubishi_encoder_data.encoder_command=0x1A;}//j2s series also gives position after this command but resolution is limited to 16-bit
			else {mitsubishi_encoder_data.encoder_command=0xA2;}
			//allow hotplug of the encoder
			mitsubishi_encoder_data.encoder_state=encoder_ok;
			if(inverter.error==encoder_error_communication){
				inverter.error=no_error;
			}
		}else{
			mitsubishi_encoder_data.encoder_state=encoder_error_no_communication;
		}

	}

}
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

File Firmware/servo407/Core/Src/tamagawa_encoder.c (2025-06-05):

/*
 * tamagawa_encoder.c
 *
 *  Created on: 12 wrz 2022
 *      Author: Wiktor
 */
#include "tamagawa_encoder.h"
#include "inverter.h"
#include <string.h>
#include "cmsis_os.h"
#include "mitsubishi_encoder.h"
#include <math.h>


extern UART_HandleTypeDef huart1;
//uint8_t UART2_RX_raw[10];
tamagawa_encoder_data_t tamagawa_encoder_data={
		.checksum_error_count=0,
		.encoder_command=0x1A,
		//command 0x02 gives position[2,3,4] and cheksum[5], 0x1A gives two positions, 0xC2 resets one-turn data, 0x92 gives two null bytes and checksum
		//five bits of command, commands are listed in https://www.ti.com/lit/ug/tidue74d/tidue74d.pdf + 010 as sink
		//status word[1] = 32 if ok 48 if error ?????
		//alarm word [9] = 192 if ok????
		.encoder_position=0,
		.encoder_state=encoder_eeprom_reading,
		.excessive_acceleration_error_count=0,
		.last_encoder_position=0,
		.motor_eeprom_request={0},
		.motor_data_response_packet={0},
		.motor_eeprom={0},
		.speed=0,
		.communication_error_count=0
};

void tamagawa_encoder_request_position(void){
	if(USART_fast_transmit_RS485(&huart1, tamagawa_encoder_data.encoder_command)!=HAL_OK){inverter_error_trip(internal_software);}
	if(HAL_UART_Receive_DMA(&huart1,(uint8_t*)&tamagawa_encoder_data.motor_data_response_packet, 11)!=HAL_OK){//start listening for response, it will be automatically copied by DMA after reception
		tamagawa_encoder_data.communication_error_count++;
		if(tamagawa_encoder_data.communication_error_count>10){inverter_error_trip(encoder_error_communication);}
	}else{tamagawa_encoder_data.communication_error_count=0;}

}
void tamagawa_encoder_process_position(void){
	uint8_t xor_cheksum=0;
	for(uint8_t i=0;i<10;i++){
		xor_cheksum^=tamagawa_encoder_data.motor_data_response_packet[i];
	}
	if(xor_cheksum!=tamagawa_encoder_data.motor_data_response_packet[10]){
		tamagawa_encoder_data.checksum_error_count++;
		if(tamagawa_encoder_data.checksum_error_count>10){inverter_error_trip(encoder_error_communication);tamagawa_encoder_data.checksum_error_count=0;}
	}
	else{ //calculate position and speed from received earlier data
		//tamagawa_encoder_data.encoder_state=encoder_ok;
		tamagawa_encoder_data.last_encoder_position=tamagawa_encoder_data.encoder_position;
		tamagawa_encoder_data.encoder_position=tamagawa_encoder_data.motor_data_response_packet[2] | tamagawa_encoder_data.motor_data_response_packet[3]<<8 | tamagawa_encoder_data.motor_data_response_packet[4]<<16;
		if(parameter_set.encoder_polarity){tamagawa_encoder_data.encoder_position=131072-tamagawa_encoder_data.encoder_position;}
		tamagawa_encoder_data.speed = tamagawa_encoder_data.last_encoder_position-tamagawa_encoder_data.encoder_position;
		inverter.encoder_raw_position=tamagawa_encoder_data.encoder_position>>1;
		inverter.rotor_electric_angle=(((fmodf(tamagawa_encoder_data.encoder_position, 131072.0f/(float)parameter_set.motor_pole_pairs))/(131072.0f/(float)parameter_set.motor_pole_pairs))*_2_PI)+parameter_set.encoder_electric_angle_correction;
		if(inverter.rotor_electric_angle>=_2_PI){inverter.rotor_electric_angle-=_2_PI;}
		if(inverter.rotor_electric_angle<0){inverter.rotor_electric_angle+=_2_PI;}
		//mechanical encoder defect detection not tested
		if(((tamagawa_encoder_data.speed>2000) && (tamagawa_encoder_data.speed<129000))|| ((tamagawa_encoder_data.speed<(-2000)) && (tamagawa_encoder_data.speed>(-129000)))){
			tamagawa_encoder_data.excessive_acceleration_error_count++;
			if(tamagawa_encoder_data.excessive_acceleration_error_count>3){tamagawa_encoder_data.encoder_state=encoder_error_acceleration;}
		}
	}
}

HAL_StatusTypeDef tamagawa_encoder_read_eeprom(uint8_t address, uint8_t * receivedByte){

	uint8_t received_data [4];
	HAL_StatusTypeDef status=HAL_OK;
	tamagawa_encoder_data.motor_eeprom_request [0] = 0xEA;
	tamagawa_encoder_data.motor_eeprom_request [1] = address;
	tamagawa_encoder_data.motor_eeprom_request [2] = tamagawa_encoder_data.motor_eeprom_request [0] ^tamagawa_encoder_data.motor_eeprom_request [1];
	status = HAL_UART_Receive_DMA(&huart1, received_data, 4);
	if(status!=HAL_OK){
		tamagawa_encoder_data.communication_error_count++;
		if(tamagawa_encoder_data.communication_error_count>10){tamagawa_encoder_data.encoder_state=encoder_error_no_communication;inverter_error_trip(encoder_error_communication);}
	}
	__disable_irq();
	HAL_GPIO_WritePin(ENCODER_DE_GPIO_Port,ENCODER_DE_Pin, 1);
	if(HAL_UART_Transmit(&huart1, tamagawa_encoder_data.motor_eeprom_request, 3, 1)){inverter_error_trip(internal_software);}
	HAL_GPIO_WritePin(ENCODER_DE_GPIO_Port,ENCODER_DE_Pin, 0);
	__enable_irq();
	osDelay(1);
	uint8_t xor_cheksum=0;
	for(uint8_t i=0;i<3;i++){
		xor_cheksum^=received_data[i];
	}
	if(xor_cheksum!=received_data[3]){status=HAL_ERROR;tamagawa_encoder_data.checksum_error_count++;}
	*receivedByte=received_data[2];


	return(status);
}

HAL_StatusTypeDef tamagawa_encoder_read_id(void){

	uint8_t received_data [4];
	HAL_StatusTypeDef status=HAL_OK;
	status = HAL_UART_Receive_DMA(&huart1, received_data, 4);
	if(status!=HAL_OK){
		tamagawa_encoder_data.communication_error_count++;
		if(tamagawa_encoder_data.communication_error_count>10){tamagawa_encoder_data.encoder_state=encoder_error_no_communication;inverter_error_trip(encoder_error_communication);}
	}
	uint8_t command=0x92;
	__disable_irq();
	HAL_GPIO_WritePin(ENCODER_DE_GPIO_Port,ENCODER_DE_Pin, 1);
	if(HAL_UART_Transmit(&huart1, &command, 1, 1)){inverter_error_trip(internal_software);}
	HAL_GPIO_WritePin(ENCODER_DE_GPIO_Port,ENCODER_DE_Pin, 0);
	__enable_irq();
	osDelay(5);
	uint8_t xor_cheksum=0;
	for(uint8_t i=0;i<3;i++){
		xor_cheksum^=received_data[i];
	}
	if(xor_cheksum!=received_data[3]){status=HAL_ERROR;tamagawa_encoder_data.checksum_error_count++;}else{
		tamagawa_encoder_data.encoder_id[0]=received_data[1];
		tamagawa_encoder_data.encoder_id[1]=received_data[2];}

	return(status);
}

HAL_StatusTypeDef tamagawa_encoder_write_eeprom(uint8_t address, uint8_t data){
	uint8_t data_to_send [4];
	uint8_t received_data[4];
	HAL_StatusTypeDef status = HAL_OK;
	if(address>80){status = HAL_ERROR;}else{
		data_to_send[0]=0x32;
		data_to_send[1]=address;
		data_to_send[2]=data;
		data_to_send[3]=data_to_send[0]^data_to_send[1]^data_to_send[2];
		status = HAL_UART_Receive_DMA(&huart1, received_data, 4);
		if(status!=HAL_OK){
			tamagawa_encoder_data.communication_error_count++;
			if(tamagawa_encoder_data.communication_error_count>10){tamagawa_encoder_data.encoder_state=encoder_error_no_communication;inverter_error_trip(encoder_error_communication);}
		}else{
			HAL_GPIO_WritePin(ENCODER_DE_GPIO_Port,ENCODER_DE_Pin, 1);
			if(HAL_UART_Transmit(&huart1, data_to_send, 4, 1)){inverter_error_trip(internal_software);}
			HAL_GPIO_WritePin(ENCODER_DE_GPIO_Port,ENCODER_DE_Pin, 0);
		}
		osDelay(10);
		if(received_data[1]!=address ||received_data[2]!=data || received_data[3]!=(received_data[0]^received_data[1]^received_data[2])){
			status=HAL_ERROR;
		}
	}
	return status;

}
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

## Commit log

2023-01-19 folder change
    [10A6.PcbLib, 10A6.SchLib, 5pin_SO6_z90.stp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]
2023-01-19 pcb layout
    [servo_pwr.PcbDoc]
2023-01-21 pcb work
    [GBJ2506.PcbLib, Infineon IPM.PcbLib, STGW30NC60KD.PcbLib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]
2023-02-22 pcb routing
    [CRL5W-33k.SchLib, DClink.SchDoc, resistor 5w.PcbLib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]
2023-02-27 cpu board
    [display.kicad_sch, eeprom.kicad_sch, power.kicad_sch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]
2023-02-27 cpu pcb
    [connectivity.kicad_sch, display.kicad_sch, encoder.kicad_sch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]
2023-02-28 cpu schematic
    [connectivity.kicad_sch, display.kicad_sch, encoder.kicad_sch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]
2023-03-06 CPU schematic done
    [connectivity.kicad_sch, display.kicad_sch, eeprom.kicad_sch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]
2023-03-09 cpu pcb layout
    [RJ45_10P_TJ3009.STEP, USB-B-S-F-B-VT.stp, connectivity.kicad_sch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]
2023-03-10 cpu pcb routing
    [display.kicad_sch, input-output.kicad_sch, power.kicad_sch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]
2023-03-10 cpu board done
    [servo_cpu.csv, servo_cpu.kicad_pcb]
2023-03-22 inverter output voltage synthesis WIP
2023-04-17 output voltage synthesis is progress
2023-04-18 HOT ADC communication
2023-04-18 pwm modulation WIP
2023-06-07 foc and mitsubishi encoder implemented
2023-06-07 fixed bug in hot adc, disabled mitsubishi encoder
    disabled mitsubishi encoder because it was not working and also causing issues with SPI2 DMA for hot adc
    [comm_modbus.c, inverter.c, inverter.h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]
2023-06-08 hot adc fixed
    mitsubishi sometimes does not initialize
    [inverter.c, main.c, mitsubishi_encoder.c]
2023-06-08 mitsubishi encoder and speed limiter
2023-06-11 abz encoder implemented
2023-06-21 modbus usb rework and softstart delay added
    [comm_modbus.c, inverter.c, inverter.h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]
2023-06-21 led status reporting implemented
2023-06-29 mitsubishi encoder resolution change
2023-06-30 abz encoder polarity switch added
2023-07-05 panasonic minas encoder support
2023-07-23 tamagawa encoder slight rework
    [inverter.c, main.c, servo407.ioc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]
2023-07-25 fix for mitsubishi j2 encoders
    j2 encoder doesnt work over 5kHz
    [comm_modbus.c, inverter.c, inverter.h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]
2023-07-25 current measurement noise filtered
    [comm_modbus.c, inverter.c, main.c]
2023-07-26 delta encoder in progress
2023-08-03 current controller tuning
2023-09-21 motor control loop execution speed optimized
2023-09-23 tamagawa encoder bugfix
2023-10-07 Revert "new control modes implemented"
    This reverts commit 8d178d27cb936a9ae3871c2e015a36b752bb5537.
    [comm_modbus.c, inverter.c, inverter.h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]
2023-11-02 speed ramp generator fixed
    [inverter.c, parameter_list.c]
2023-11-02 Revert "Merge branch 'main' into new-parameter-set"
    This reverts commit baf1e8bbb4a0091322eba564e62bccc52cc87168, reversing
    changes made to 4cd528f12005d2d23f4941173ab873df024b014f.
    [comm_modbus.c, inverter.c, inverter.h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]
2023-11-04 Tamagawa encoder direction flip
    [tamagawa_encoder.c]
2023-11-29 output voltage compensation improved
2023-12-27 current controller performance improved
2024-01-15 fixed motor noise when heavy reading from USB
    [servo407.ioc]
2024-02-23 switched oled_ck pin for swo debug option on DAC2
2024-02-26 CANbus control working in pp and pv modes
2024-10-18 abz encoder bugfix
2024-11-07 abz encoder debugged and improved
2024-11-08 mitsubishi encoder variable comm frequency added
2025-04-01 output voltage calculation bugfix
    [delta_encoder.c, inverter.c, inverter.h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]
2025-04-07 delta encoder added acceleration detection
2025-04-07 delta encoder acceleration error trip
    [delta_encoder.c]
2025-06-05 tamagawa encoder response decoding
2025-07-22 omnuc g encoder support prototype

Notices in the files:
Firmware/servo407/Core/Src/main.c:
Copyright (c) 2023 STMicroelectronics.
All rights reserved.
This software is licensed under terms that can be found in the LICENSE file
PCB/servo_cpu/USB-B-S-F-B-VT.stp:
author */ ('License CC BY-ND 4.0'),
